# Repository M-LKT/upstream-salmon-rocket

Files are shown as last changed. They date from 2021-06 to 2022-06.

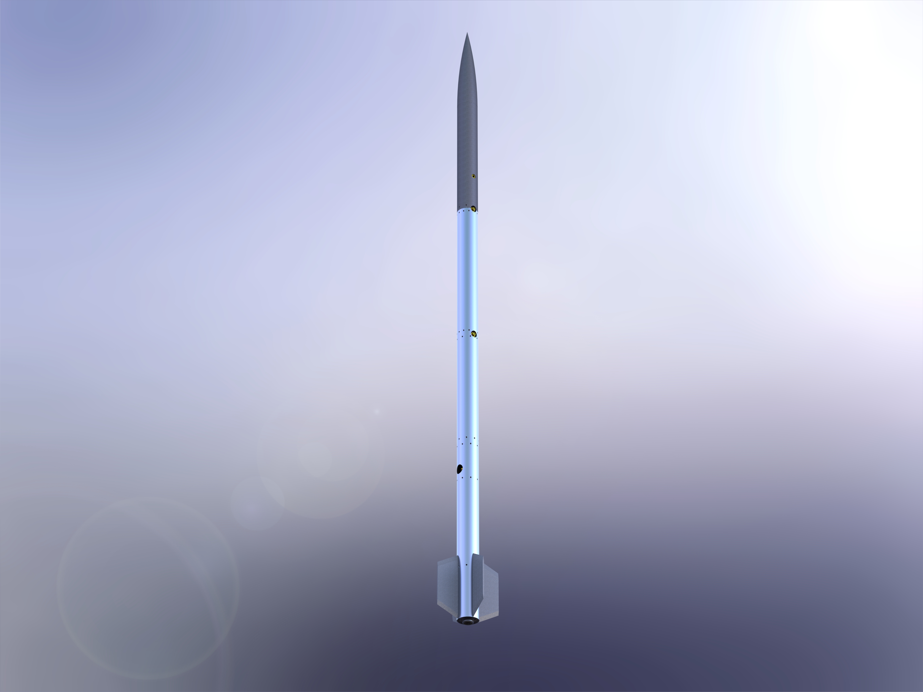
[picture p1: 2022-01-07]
renders/design-beta_v1.0.JPG

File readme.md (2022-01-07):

# Interfaces for Your Engine -> MicroLiquid Vehicle

## Dimensions
- Rocket Tube OD: 2in
- Rocket Tube Thickness: 0.049in
- Standard Skin Fastener: [M2x0.4 Countersunk Torx](https://www.mcmaster.com/92703A146/), 8mm; 8X or 12X
- 

# Other values
- Nitrogen initial pressure: ~1000psi
- Flow control orifice (you choose): [Threaded Flow Control Orifice with Brass Body Plug with Hex Socket, 1/8 NPT Male](https://www.mcmaster.com/2712T51/) (might switch to UNF thread based on burst disk design)
- Target Liftoff TWR: 5
- Estimated takeoff weight: 8.5 lb
- Estimated dry weight: 5 lb

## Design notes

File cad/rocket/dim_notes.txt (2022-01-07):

0.528117in center - vent
0.240000in inlet - vent
0.026500in extra pneu fit gap to piston
1.3745in bore depth
ORB 3/8-24

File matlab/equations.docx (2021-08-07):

Mass lost over time:

m(t)= ∫_0^t (dm)/(dt) dt=̇_0^t m dt

Mass flowrate with pressure:

m=ρQ=ρC_d A√(2Δp)

Pressure with mass

p=(p_i V_i)/V=(p_i V_i)/(V_i +m/ρ)

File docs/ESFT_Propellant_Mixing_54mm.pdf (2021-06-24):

# Eagle Space Flight Team 54mm Propellant Mixing Procedure

### Rev. 1 – 2/25/15

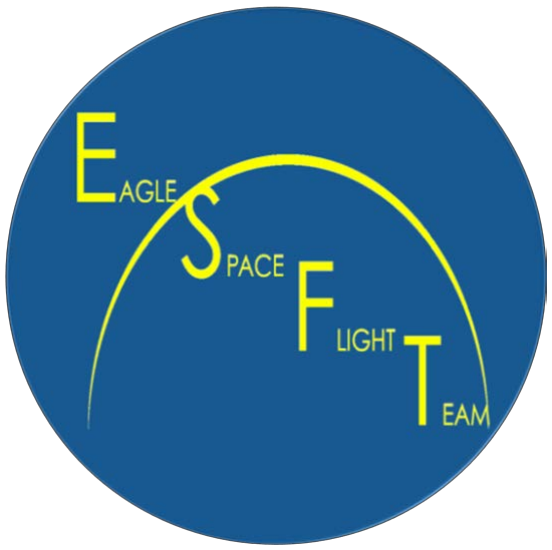
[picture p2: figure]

## Introduction

This document is a procedure for the mixing and processing of large (multiple pounds) batches of ammonium perchlorate composite propellant (APCP) for use in amateur rocket motors. Its purpose is to provide a means for the Propulsion Group of the Eagle Space Flight Team (ESFT) to safely produce a consistent, reliable solid rocket propellant for use on ESFT’s rocket test flights leading up to and including an attempt at a suborbital spaceflight. This version of the document, specifically, is tailored to the mixing and processing of propellant for the 54mm -diameter motors we will use to perform a ballistic characterization of our propellant. These motors will each contain approximately 2lb of propellant, and each individual motor will be mixed as one batch of propellant.

## Method

For mixing the propellant, the team will use a 6qt KitchenAid mixer. Its powerful motor, sturdy construction, and reliability have made this particular mixer the standard in amateur rocketry circles. To avoid generating excess heat during mixing, the mixer is run at a moderate speed, just fast enough to prevent the thickness of the propellant from causing the motor to seize and burn out.
After mixing, the bowl of propellant will be fitted with an acrylic lid attached to a vacuum pump. The vacuum pump will then be used to pull a light vacuum on the contents of the mixing bowl. This will remove any air bubbles introduced into the propellant during mixing as well as any trapped gas from the curing process of the propellant’s binder.
After vacuum processing, the propellant will be packed into cardboard casting tubes with an aluminum mandrel in the center. Each propellant grain will be cast individually, eliminating the need for any cutting or drilling of the propellant after curing.

## Safety

Safety of those working with propellant is the highest priority of any propellant manufacturing operation. During the entire propellant mixing process, all personnel will wear eye protection. Those working directly with propellant chemicals will wear nitrile gloves, and all personnel will wear dust masks during the measuring and incorporation of the dry components of the propellant. Those working directly with propellant will wear non-loose fitting clothing made of cotton or wool (No synthetics!), and long hair will be tied back.
In order to account for the extremely unlikely event of the propellant igniting during mixing, the mixer will not be located inside while it is running. Instead, it will be located a safe distance from the building on the end of an extension cord. The mixer’s speed will be set with it powered off. It will then be switched on and off by inserting and removing the end of the extension cord plugged into a wall socket a safe distance away.
In order to keep dust to a minimum, dry propellant chemicals will be added with the mixer powered off and gently incorporated by hand until they are sufficiently wetted out to prevent any dust from being kicked up when the mixer is restarted. No team members will stand near the mixer while it is switched on and off, and monitoring of the mixing process will take place with a Lexan blast shield between any personnel and the mixer.
During all mixing operations, one person will constantly man a chemical fire extinguisher (No water-filled “pump cans”!), and another will man the point where the extension cord plugs into a wall outlet. In the extremely unlikely event of the propellant igniting during mixing, all team members will move away from the mixer and the person manning the wall outlet will immediately power off the mixer. The mixer, which will be a safe distance from any structures or personnel, will then be allowed to burn until all propellant in the mixing bowl has been consumed. It is only at that time that the person with the fire extinguisher will attempt to put out any remaining fires fueled by parts of the mixer itself.
After mixing, vacuum processing, and packing of the propellant is complete, it will be allowed to cure in a fire cabinet designated for solid rocket propellant and other self-oxidizing materials. After the propellant has cured and the mandrel has been removed, the propellant will continue to be stored in the same cabinet until it is needed for static testing or flight. Mix sessions will be scheduled such that this storage interval is as short as is feasible.

## Personnel

The personnel present for any mixing session will be assigned to one of the following duties.

- Chemical Measuring: Weighs out precise amounts propellant chemicals into temporary containers before mixing starts. This makes the mixing operation itself run more smoothly.
- Ingredient Incorporation/Mix Observer: Adds propellant chemicals to mixing bowl one at a time in the order presented later in this document. Occasionally checks propellant during mixing to ensure that it is being mixed thoroughly enough to produce a consistent product.
- Mixer Power Operator: Mans the location where the mixer plugs into a wall outlet. Switches mixer on and off as needed during mixing and remains ready to switch off mixer in unlikely event of propellant ignition.
- Fire Extinguisher Operator: Stands ready with fire extinguisher. In unlikely event of propellant ignition, they will wait until propellant has been fully consumed before extinguishing remains of mixer.
- Safety Observer: Watches area surrounding mixing operation for safety hazards. Keeps unrelated personnel a safe distance away from mixing operation.
The setup for propellant mixing will be arranged similarly to the diagram on the next page.

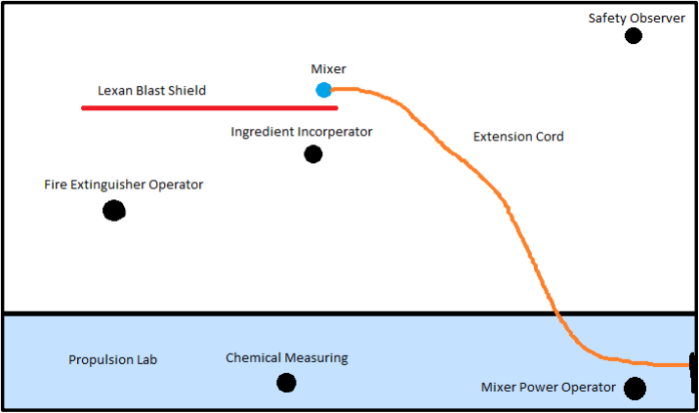
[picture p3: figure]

In this setup, all personnel have either a blast shield, building wall, or sufficient offset distance between themselves and the mixer at all times. Sufficient offset distance is considered to be at least 30ft without a blast shield or wall.

## Procedure

### Propellant Formula

The propellant formula to be used by the team consists of the following components.

- 200µ Ammonium Perchlorate: The propellant’s oxidizer
- 20µ Atomized Spherical Aluminum Powder: The propellant’s fuel
- 5µ Oxamide: Burn rate suppressant.
- R-45M Hydroxyl-terminated Polybutadiene Resin (HTPB): The propellant’s binder. Also serves as a fuel.
- Desmodur E744/MDI Isocyanate: Curative for the HTPB.
- Isodecyl Pelargonate (IDP): Plasticizer for the HTPB.
- Silicone Oil: Anti-foaming agent/surfactant.
Before mixing, all personnel working with propellant must read and familiarize themselves with the MSDSs for the propellant chemicals.
These chemicals are to be mixed in the following proportions, each percentage being a portion of the desired mass of propellant to be mixed.

- Ammonium Perchlorate: 72%
- Aluminum: 7%
- Oxamide: 3%
- HTPB: 14.08%
- E744/MDI: 2.12%
- IDP: 1.8%
- Silicone Oil: One drop per kilogram of propellant being mixed

### Equipment

The following equipment is needed for each propellant mix session.

- Safety glasses
- Dust masks
- Nitrile gloves
- Lexan blast shield
- Chemical fire extinguisher
- 6qt mixer fitted with paddle
- Mixing bowl corresponding to mixer
- Ice cream spade
- Extension cord, minimum length 30’
- Vacuum pump
- Plexiglas lid fitted to bowl with fitting for vacuum pump
- Core mandrel
- Casting tube caps
- Casting tube
- Metal or wood packing rod
- Mold release spray
- Paper towels
- Mineral spirits
- Metal “burn bucket”

### Procedure

Read through this procedure in its entirety before beginning to mix!
The process of mixing propellant is both time sensitive and unforgiving of mistakes. It is imperative that all personnel know exactly what tasks to perform and exactly when to perform them.
Throughout this procedure, important safety notes will appear in boxes such as this one. Important procedural notes will appear bolded within the text.
1. Set up the mixer, extension cord, blast shield, and fire extinguisher as shown in the figure earlier in this document.

2. Cut casting tube to desired grain length. Spray coring rod and casting tube caps with mold release. Insert coring rod into bottom (non-vented) casting tube cap before sliding the casting tube over the core mandrel and seating it in the cap. Do not get mold release on the inside of the casting tube. A thorough bond between the propellant and the inside of the casting tube is imperative to proper motor operation.
The tube should fit snugly into the cap. If the casting tube fits loosely in the cap, wrap a few layers of masking tape around the bottom of the tube. If the casting tube will not fit, lightly sand the bottom of the tube.

If not wearing them already, all personnel don safety glasses at this time. All personnel in the chemical measuring area don nitrile gloves and dust masks at this time.

3. If you have not done so already, use the percentages in the propellant formula earlier in the document to calculate the mass of each component needed for the desired amount of propellant to be mixed. Double and triple check your calculations before moving forward.
4. Measure the ammonium perchlorate, aluminum, oxamide, curative, and plasticizer into separate disposable containers.

Ammonium perchlorate and aluminum are never to be allowed to come into contact without the binder!
The binder acts as a burn rate suppressant for the ammonium perchlorate/aluminum mixture and also increases the activation energy of the propellant. With the binder, this mixture will burn at approximately the same rate as office paper and requires a substantial energy input to ignite. Without the binder, the mixture is virtually identical to pyrotechnic flash powder, possessing a fast burn rate and sensitivity to friction and physical shock.
5. Measure out the HTPB resin. This ingredient can be measured directly into the mixing bowl. Next, add the plasticizer and silicone oil into the bowl. Do not stir the contents of the bowl at this time. The goal is to create a pool of plasticizer on top of the resin.
6. The aluminum is then added to the bowl by pouring it into the pool of plasticizer. When pouring in the aluminum, keep its container low over the surface of the liquid in order to keep dust to a minimum. Allow the plasticizer to soak into the aluminum until it is completely wetted out. Then, gently incorporate the aluminum into the mixture by hand using the ice cream spade. Do not move on to the next step until the aluminum powder is completely wetted out and evenly distributed within the HTPB. The container into which the aluminum was measured is then discarded in normal garbage.
7. The oxamide is then added to the bowl in the same manner as the aluminum, taking care with dust prevention. It is then incorporated into the mixture by hand. The container into which the oxamide was measured is then discarded into normal garbage.

From this point on, all waste will be disposed of in the burn bucket.
Waste which has not come into contact with ammonium perchlorate is safe to dispose of in normal garbage, but any oxidizer-contaminated waste must be disposed of in the burn bucket. This waste will be burned before disposal. The procedure for burning this waste is outlined later in this procedure.
8. Approximately one third of the ammonium perchlorate is added to the bowl at this time, employing the same dust prevention practices used with the other solid components. The ammonium perchlorate is then wetted out and incorporated into the mixture by hand as before.
9. Another third of the ammonium perchlorate is then added to the bowl and wetted out by hand.
10. The final third of the ammonium perchlorate is then added to the bowl and wetted out by hand. The bowl is then placed in the mixer which is then switched on and allowed to mix the propellant for ten minutes. During this process, the mixing is stopped every few minutes in order to scrape down the sides of the mixing bowl.
11. The mixer is then stopped and the E744/MDI is added to the bowl. The mixer is then restarted and allowed to mix the propellant for 10 minutes, stopping every few minutes to scrape down the sides of the bowl.
12. The bowl is then removed from the mixer. The vacuum lid is placed on the bowl and the vacuum pump is switched on and allowed to pull vacuum on the propellant for five minutes.
13. The pump is switched off and the lid is removed. The propellant is then pulled from the bowl, rolled into “clay snakes”, and dropped into the casting tube. Occasionally, the packing rod is used to tamp down the propellant. With the packing rod, the goal is not to mash the propellant into the tube, but rather to ensure a well-packed, uniform propellant with no voids present in the grains.
14. Once the casting tube has been filled, the top (vented) casting tube cap is slid over the mandrel and seated on the top of the casting tube. If multiple grains are being cast, the next casting tube (already fitted with a non-vented bottom cap) is slid onto the mandrel and propellant packing proceeds as with the first grain.
15. Once all propellant is packed, the casting setup is placed in a fire cabinet and allowed to cure. This process will usually take a few days.
16. The mixing bowl, mixer paddle, ice cream spade, and packing rod are all thoroughly cleaned with paper towels and mineral spirits. These paper towels and any scrap propellant are disposed of in the burn bucket. After cleanup is complete, no propellant residue whatsoever may remain on any tools or equipment.

17. After cleanup is complete, the burn bucket is taken to a remote area away from combustible materials. Its contents are then ignited either electronically or using a fuse and allowed to burn completely. The ashes left over are then doused with water and disposed of in normal garbage.

Firefighting measures must be in place when burning the contents of the burn bucket!
This includes at least two people and at least one chemical fire extinguisher. Shovels and/or rakes are also useful for firefighting.
18. After three to five days, the propellant should be fully cured. The casting tube caps can now be removed and the core mandrels pulled out of the grains. The propellant is to be stored in a fire cabinet until use.

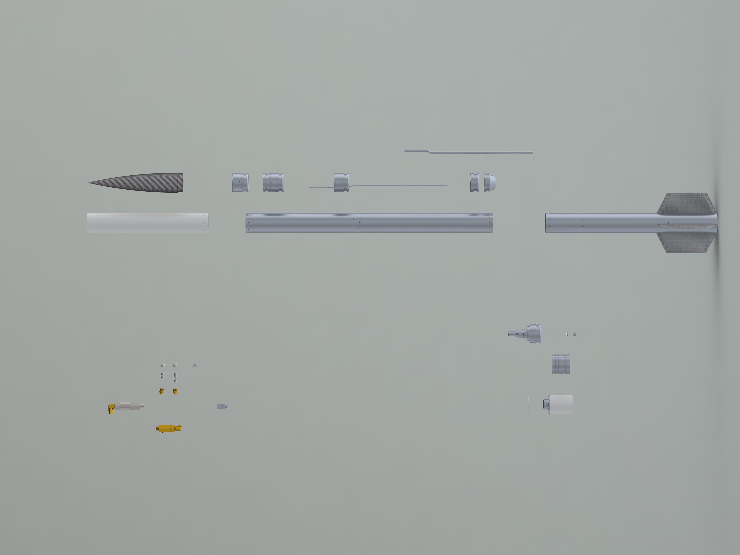
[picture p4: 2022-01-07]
renders/exploded.JPG

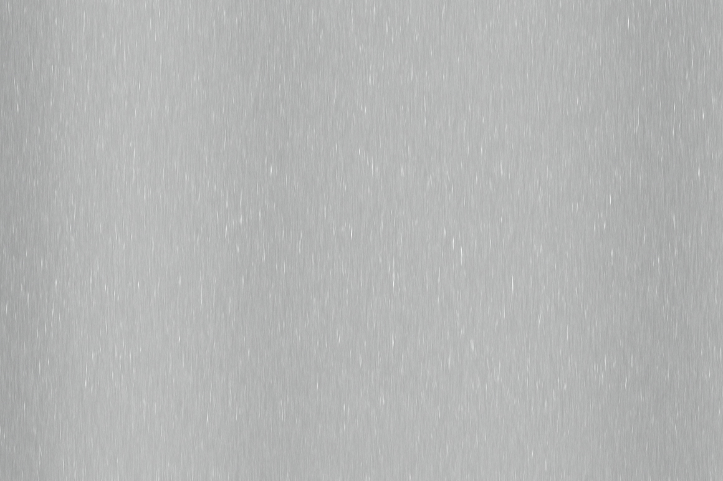
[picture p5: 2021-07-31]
vehicle-sims/aluminum-texture-1.jpg

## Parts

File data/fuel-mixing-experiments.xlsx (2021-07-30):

Type | Salmon Mass | IPA Mass | Salmon % | Total Mass | Pre-Mix Vol | Mix Time | Post-Mix Vol | Post-Mix Mass | Notes | Density
F/W | g | g | ratio | g | mL | s | mL | g
F | 41.4 | 55.2 | 0.4285714286 |  |  |  | 25 | 21 |  | 0.84
 |  | 61.7 | 0 |  |  |  | 30 | 27.8 |  | 0.9266666667
 |  |  | #DIV/0!
 |  |  | #DIV/0!
 |  |  | #DIV/0!
 |  |  | #DIV/0!
 |  |  | #DIV/0!
 |  |  | #DIV/0!

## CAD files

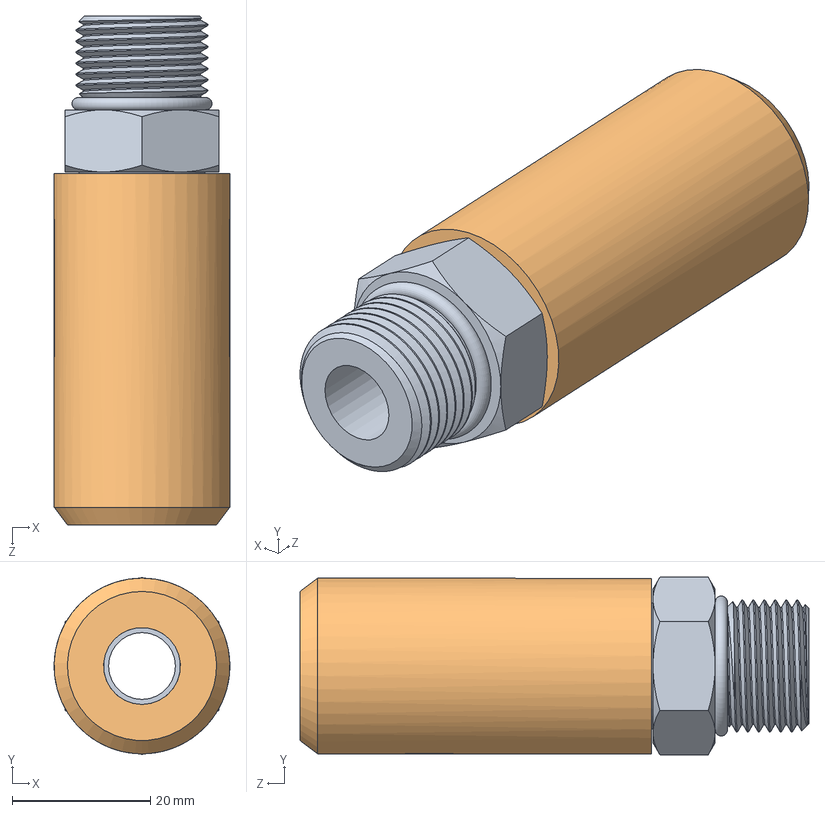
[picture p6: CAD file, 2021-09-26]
cad/burst_disk/normal_burst.SLDASM
25.4 x 25.7 x 73.5 mm
6407T859_O-Ring Face Seal Fitting
test_burst-disk

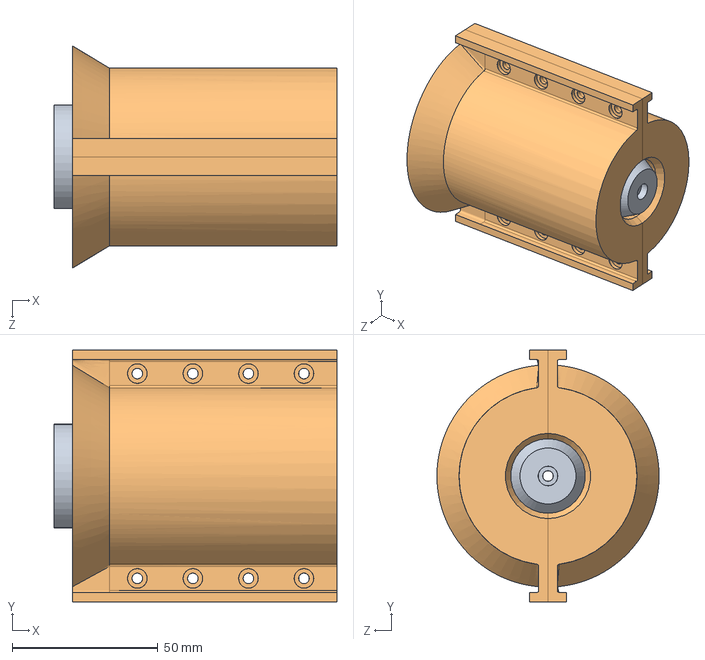
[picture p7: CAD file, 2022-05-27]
cad/engines/mold.SLDASM
97.0 x 86.4 x 76.2 mm
cast-with-nozzle_MOLD_chamber-core
cast-with-nozzle_MOLD_outer x 2

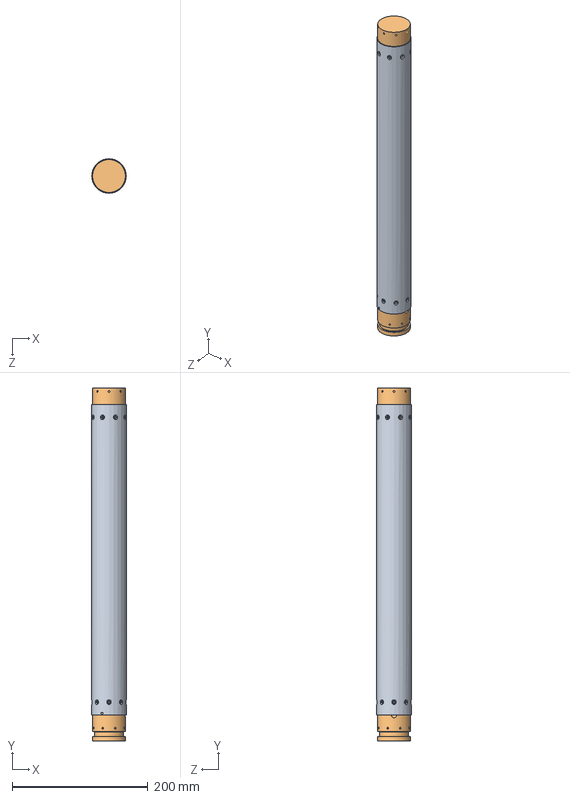
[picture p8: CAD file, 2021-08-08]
cad/rocket/sw_fea/press-sim-assy.SLDASM
50.8 x 519.4 x 50.8 mm
tube
spacer x 2

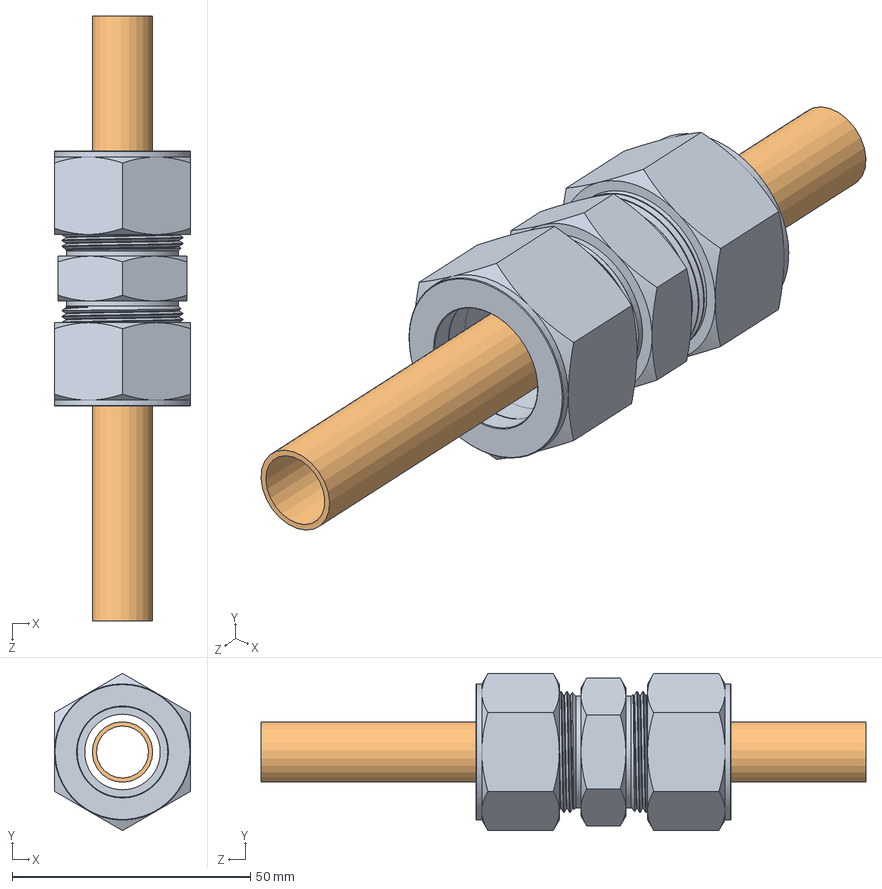
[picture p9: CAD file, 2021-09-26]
cad/burst_disk/concentric_burst.SLDASM
28.6 x 33.0 x 127.0 mm
5182K722_Yor-Lok Fitting for Stainless Steel Tubing
0.5-tube

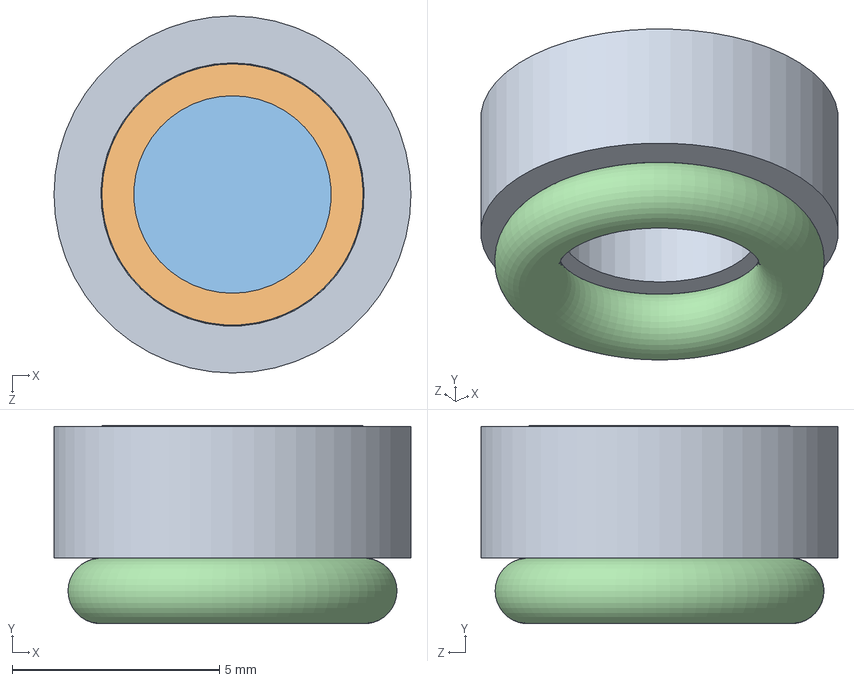
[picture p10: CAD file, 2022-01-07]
cad/rocket/burst_disk/Burst_Assembly.SLDASM
8.61 x 4.78 x 8.61 mm
burst-housing
disk-compressor
disk-proxy
AS568-006-O-Ring

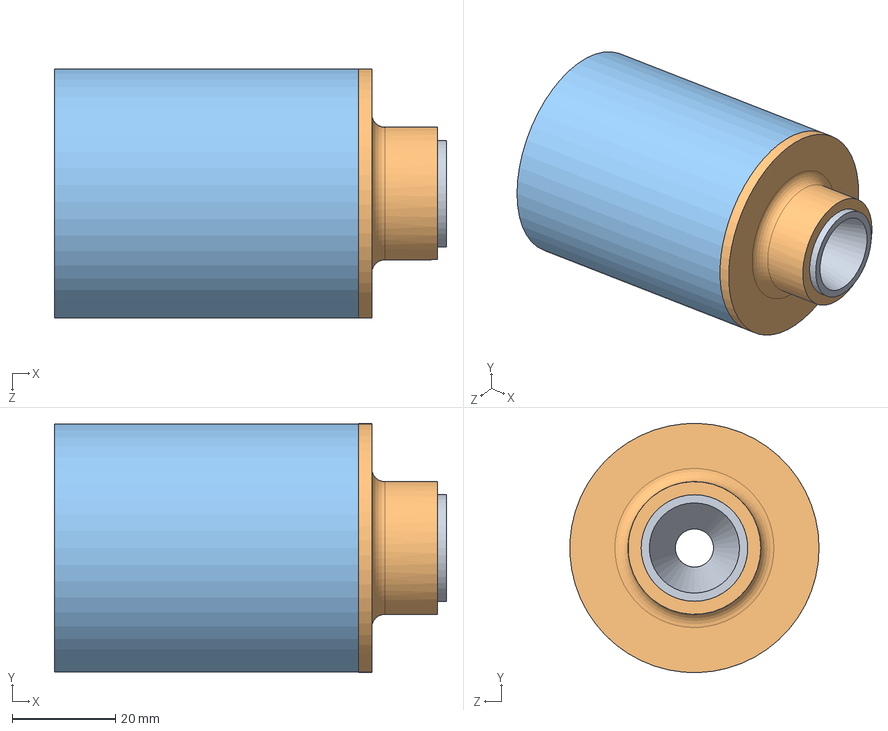
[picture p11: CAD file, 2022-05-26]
cad/engines/Engine-Retainer_config.SLDASM
76.0 x 48.3 x 48.3 mm
RCS-0.291-Nozzle
retainer-cap^Engine-Retainer_config
cast-with-nozzle

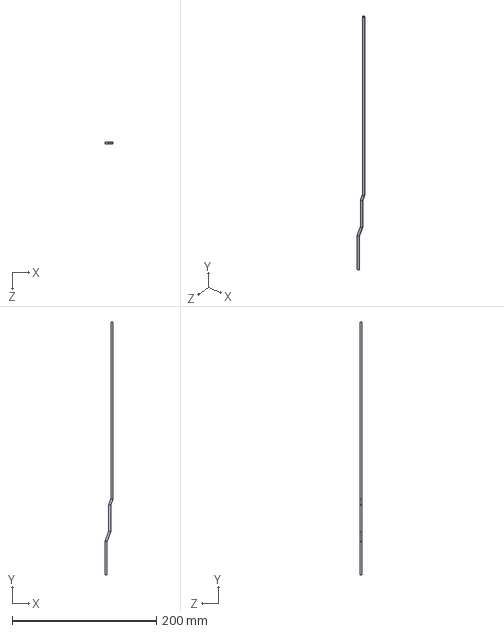
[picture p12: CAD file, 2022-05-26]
cad/rocket/Tube_2-Rocket.SLDASM
11.3 x 350.5 x 3.18 mm

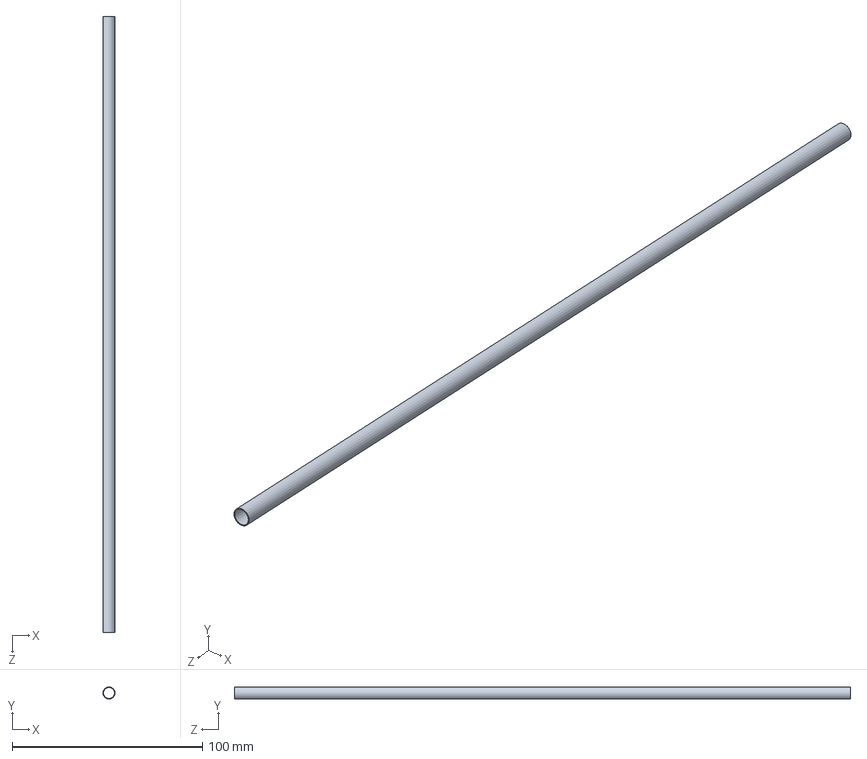
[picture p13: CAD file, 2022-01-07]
cad/rocket/main-lox-tube.SLDPRT
6.35 x 6.35 x 323.9 mm

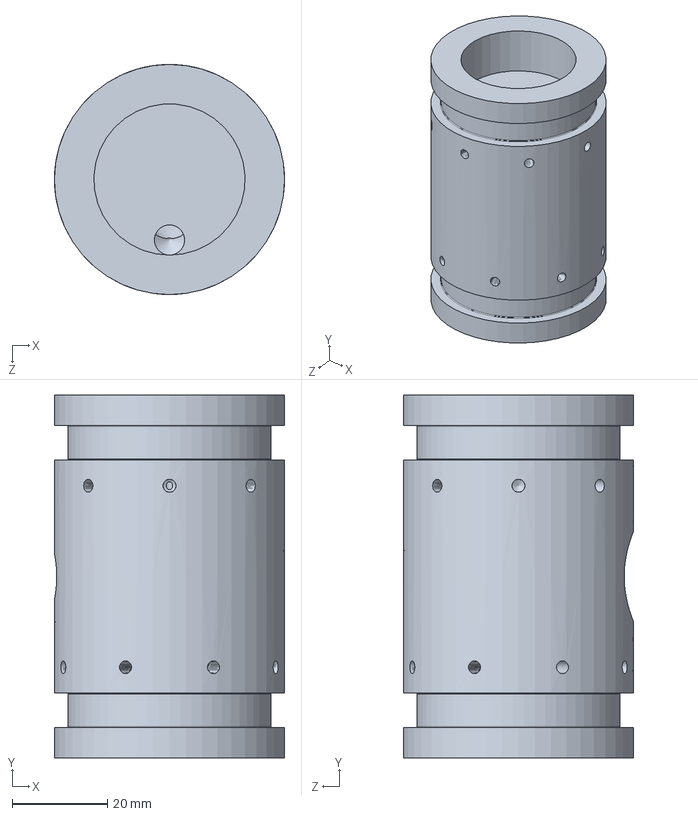
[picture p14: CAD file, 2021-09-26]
cad/rocket/valve_test_assy.SLDASM
48.3 x 76.2 x 48.3 mm
spacer
ball
seat x 2
valve-cap

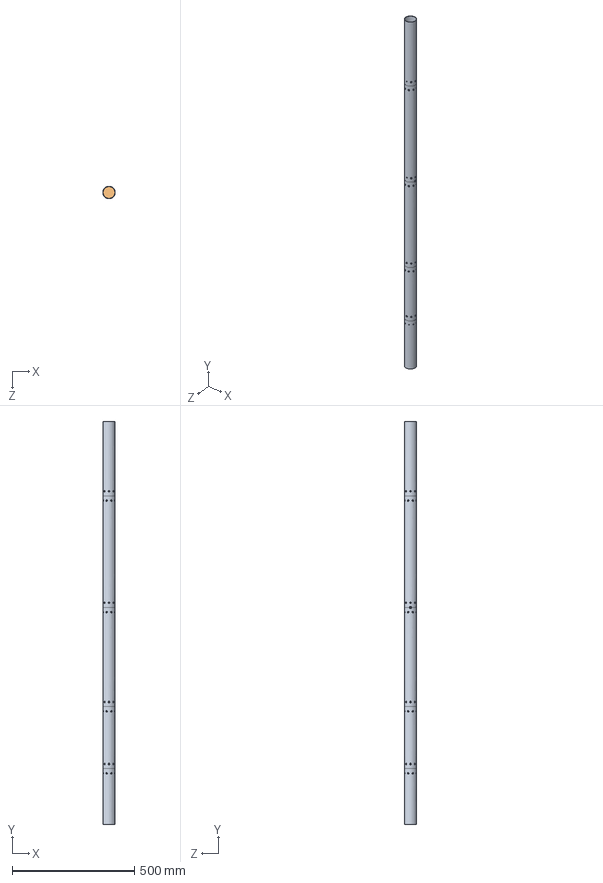
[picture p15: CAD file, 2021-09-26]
cad/rocket/Rocket.SLDASM
50.8 x 1651.0 x 50.8 mm
tube x 5
spacer x 4
94355A231_NONMARRING FLAT POINT SOCKET SET SCREW (5-16 length)
94564A405_NYLON HEX SOCKET FLAT POINT SET SCREW
pyro-valve-piston
injector
ablative-chamber

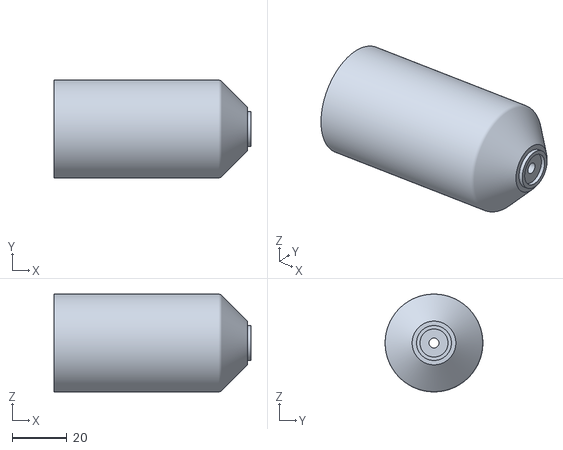
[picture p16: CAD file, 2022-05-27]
cad/engines/mold-with-nozzle-v2/BOTTOM-cast-with-nozzle_MOLD_chamber-core.STL
71.6 x 35.6 x 35.6

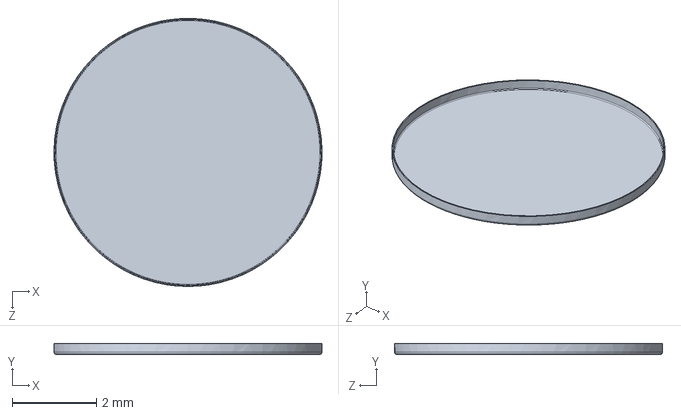
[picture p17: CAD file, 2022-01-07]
cad/rocket/burst_disk/disk-proxy.SLDPRT
6.35 x 0.254 x 6.35 mm

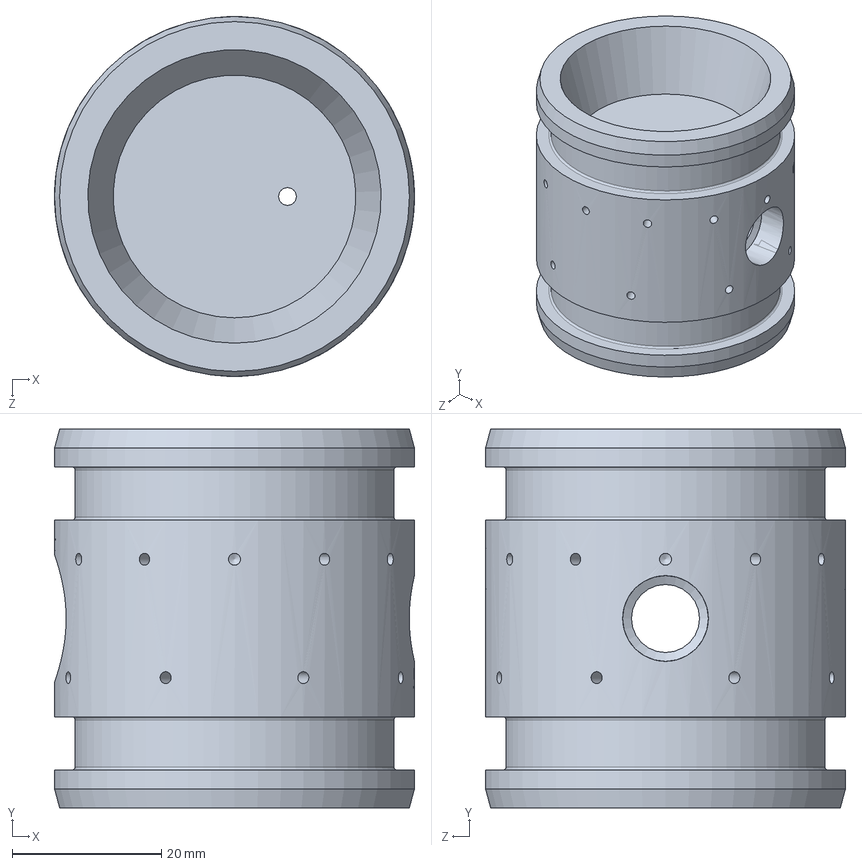
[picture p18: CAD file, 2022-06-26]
cad/rocket/spacer.SLDPRT
48.3 x 50.8 x 48.3 mm

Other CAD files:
cad/rocket/Tube_4-Rocket.SLDASM
cad/rocket/Auto-Main_LOX-Rocket.SLDASM
cad/rocket/Tube_3-Rocket.SLDASM
cad/rocket/Tube_3-Rocket-001.SLDASM
cad/rocket/Tube_1-Rocket.SLDASM
cad/burst_disk/0.5-tube.SLDPRT
cad/burst_disk/5182K722_Yor-Lok Fitting for Stainless Steel Tubing.SLDPRT
cad/burst_disk/6407T859_O-Ring Face Seal Fitting.SLDPRT
cad/burst_disk/test_burst-disk.SLDPRT
cad/cots/2333N129_Nickel-Plated Brass Push-to-Connect Fitting.SLDPRT
cad/cots/2712T655_Threaded Flow Control Orifice with Brass Body.SLDPRT
cad/cots/2712T666_Threaded Flow Control Orifice with Brass Body.SLDPRT
cad/cots/2840K21_316 Stainless-Steel Panel-Mount On Off Valve.SLDPRT
cad/cots/2840K23_316 Stainless-Steel Panel-Mount On Off Valve.SLDPRT
cad/cots/4112T53_Compact High-Pressure Brass Ball Valve.SLDPRT
cad/cots/4114T43_Brass Panel-Mount On Off Valve.SLDPRT
cad/cots/4118T114_Panel-Mount On Off Valve.SLDPRT
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

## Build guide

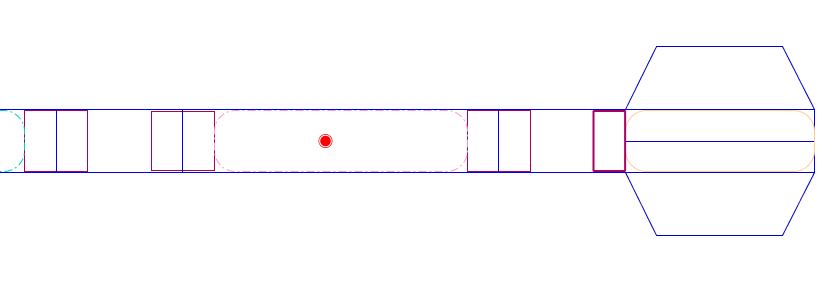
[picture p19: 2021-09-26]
cad/burst_disk/lower_assembly.png

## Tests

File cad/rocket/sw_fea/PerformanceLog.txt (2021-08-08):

Number of Contacts: 4
Number of contact data: 12992

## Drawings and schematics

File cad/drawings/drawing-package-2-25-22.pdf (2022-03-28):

2

B

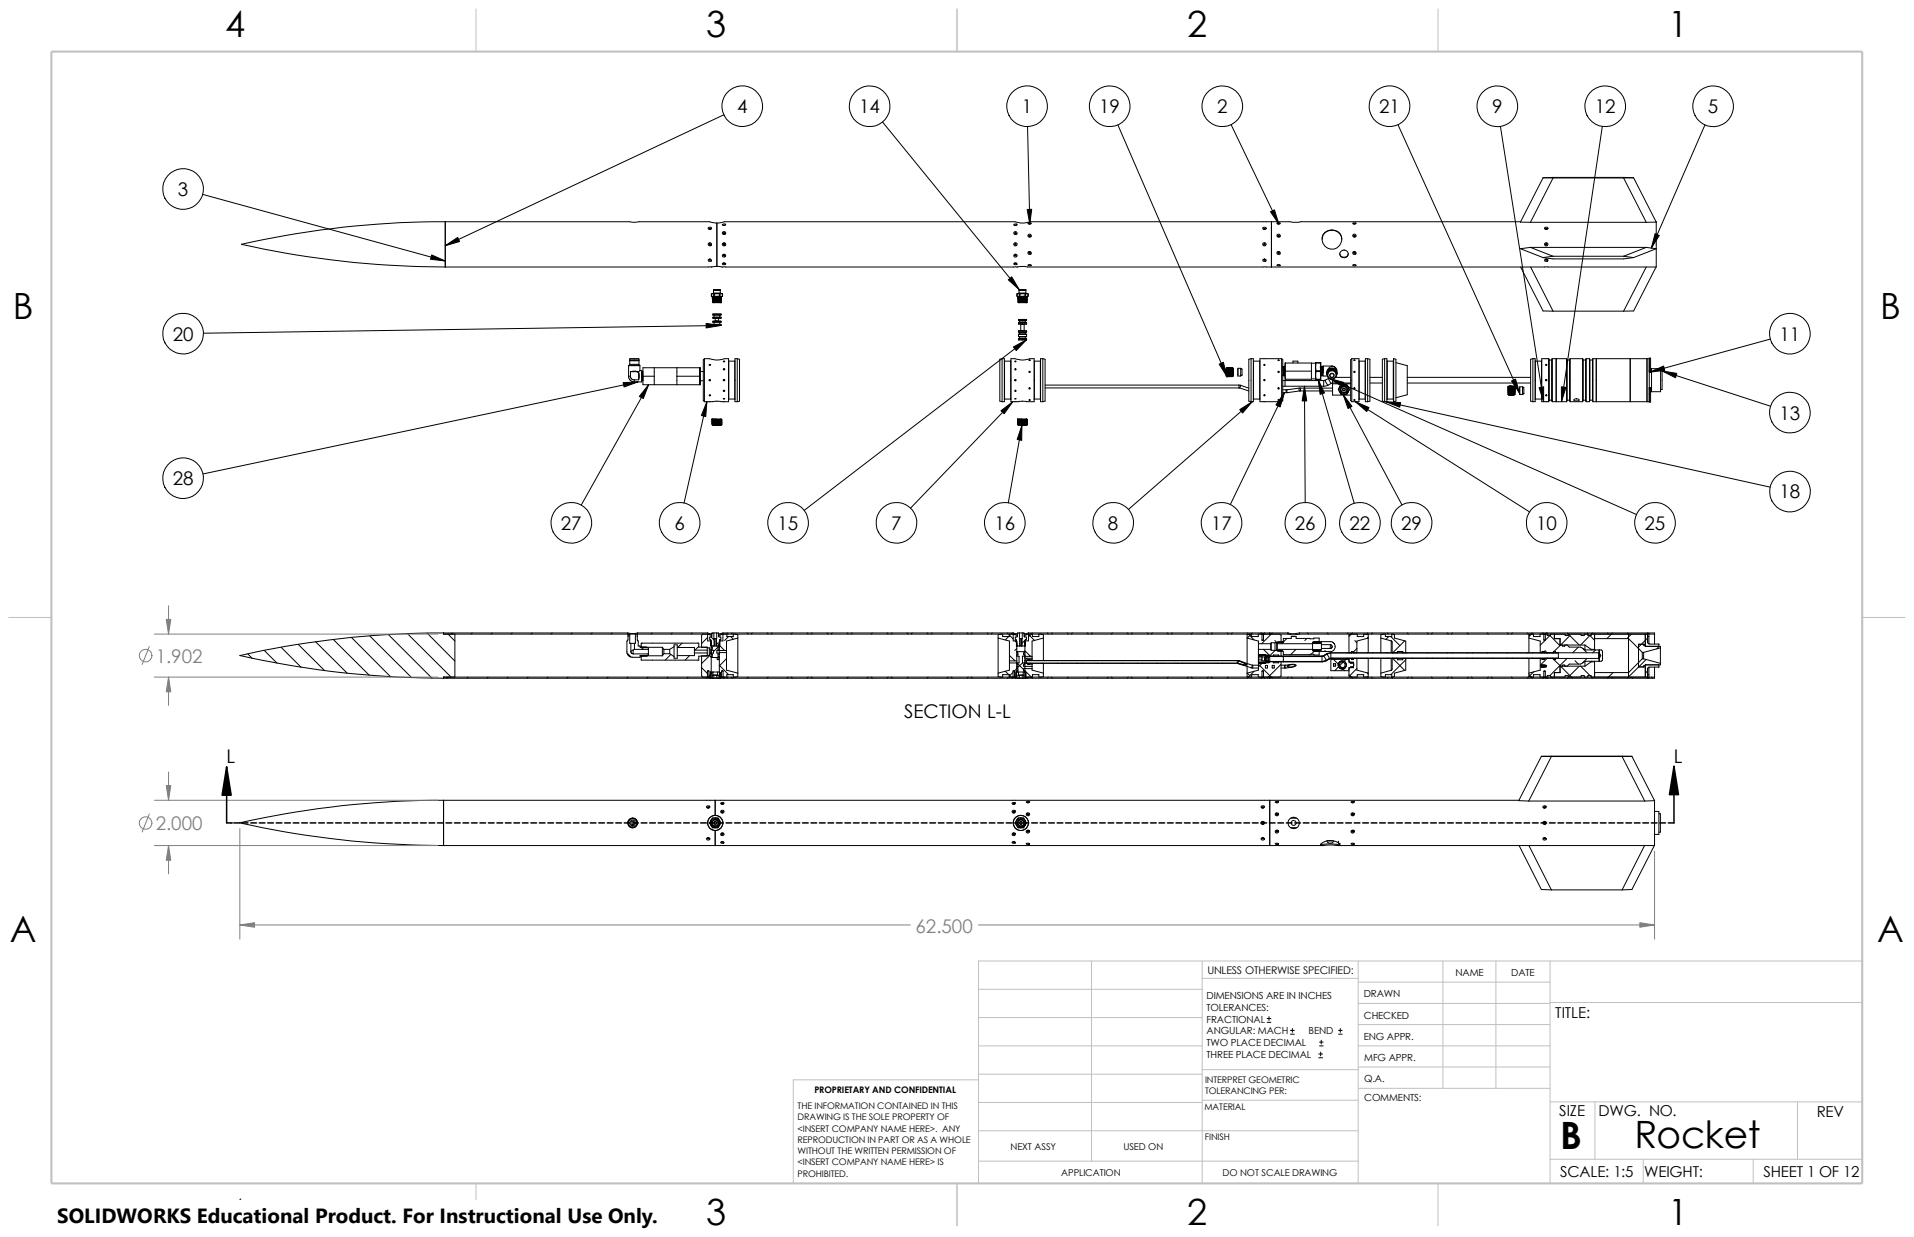
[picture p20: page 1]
SHEET 1 OF 12; SCALE: 1:5; WEIGHT:; COMMENTS:; PROHIBITED.; APPLICATION; SECTION L-L

UNLESS OTHERWISE SPECIFIED: | | NAME | DATE

DIMENSIONS ARE IN INCHES TOLERANCES: FRACTIONAL ANGULAR: MACH BEND TWO PLACE DECIMAL THREE PLACE DECIMAL | DRAWN

CHECKED | | | TITLE:

ENG APPR.
MFG APPR.

INTERPRET GEOMETRIC TOLERANCING PER: | Q.A.
MATERIAL | | SIZE B | DWG. NO. Rocket | REV

PROPRIETARY AND CONFIDENTIAL
THE INFORMATION CONTAINED IN THIS
DRAWING IS THE SOLE PROPERTY OF
<INSERT COMPANY NAME HERE>. ANY
REPRODUCTION IN PART OR AS A WHOLE
WITHOUT THE WRITTEN PERMISSION OF
<INSERT COMPANY NAME HERE> IS

NEXT ASSY | USED ON | FINISH

DO NOT SCALE DRAWING

SOLIDWORKS Educational Product. For Instructional Use Only.

B B

ITEM NO. | PART NUMBER | DESCRIPTION | QTY. | ITEM NO. | PART NUMBER | DESCRIPTION | QTY.

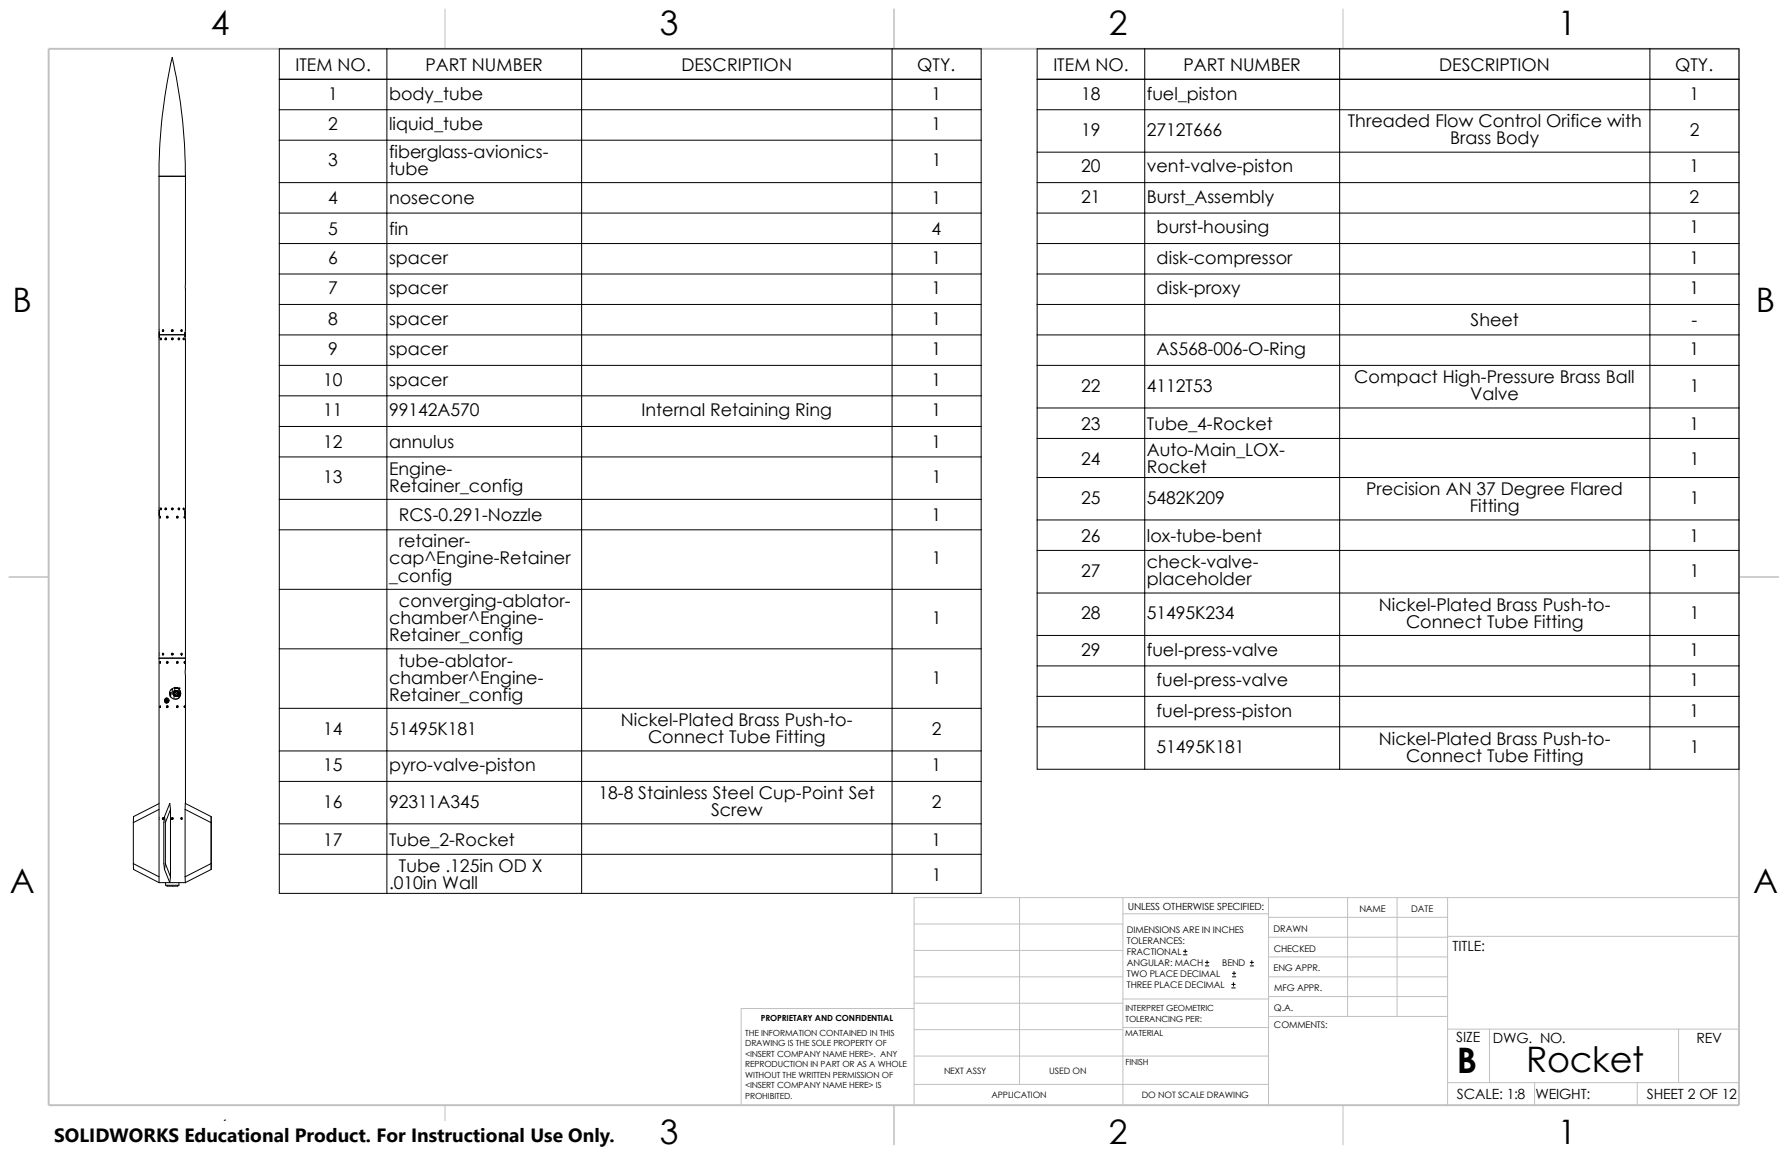
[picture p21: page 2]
Rocket; SHEET 2 OF 12; SCALE: 1:8; WEIGHT:; DWG. NO.; REV; SIZE; COMMENTS:; MATERIAL; APPLICATION; PROHIBITED.

1 | body_tube | | 1 | 18 | fuel_piston | | 1
2 | liquid_tube | | 1 | 19 | 2712T666 | Threaded Flow Control Orifice with Brass Body | 2
3 | fiberglass-avionics-tube | | 1

20 | vent-valve-piston | | 1

4 | nosecone | | 1 | 21 | Burst_Assembly | | 2
5 | fin | | 4 | | burst-housing | | 1
6 | spacer | | 1 | | disk-compressor | | 1
7 | spacer | | 1 | | disk-proxy | | 1
8 | spacer | | 1 | | | Sheet | -
9 | spacer | | 1 | | AS568-006-O-Ring | | 1
10 | spacer | | 1 | 22 | 4112T53 | Compact High-Pressure Brass Ball Valve | 1
11 | 99142A570 | Internal Retaining Ring | 1
12 | annulus | | 1
13 Engine- | Retainer_config | | 1

23 | Tube_4-Rocket | | 1
24 Auto-Main_LOX- | Rocket | | 1
25 | 5482K209 | Precision AN 37 Degree Flared Fitting | 1

RCS-0.291-Nozzle | | 1
retainer-cap^Engine-Retainer _config | | 1

26 | lox-tube-bent | | 1
27 check-valve- | placeholder | | 1

converging-ablator-chamber^Engine-Retainer_config | | 1

28 | 51495K234 | Nickel-Plated Brass Push-to-Connect Tube Fitting | 1

29 | fuel-press-valve | | 1

tube-ablator-chamber^Engine-Retainer_config | | 1

fuel-press-valve | | 1
fuel-press-piston | | 1
51495K181 | Nickel-Plated Brass Push-to-Connect Tube Fitting | 1

14 | 51495K181 | Nickel-Plated Brass Push-to-Connect Tube Fitting | 2

15 | pyro-valve-piston | | 1
16 | 92311A345 | 18-8 Stainless Steel Cup-Point Set Screw | 2

17 | Tube_2-Rocket | | 1

Tube .125in OD X .010in Wall | | 1

UNLESS OTHERWISE SPECIFIED: | | NAME | DATE

DIMENSIONS ARE IN INCHES TOLERANCES: FRACTIONAL ANGULAR: MACH BEND TWO PLACE DECIMAL THREE PLACE DECIMAL | DRAWN

CHECKED | | | TITLE:

ENG APPR.
MFG APPR.

INTERPRET GEOMETRIC TOLERANCING PER: | Q.A.

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

B B

1.282

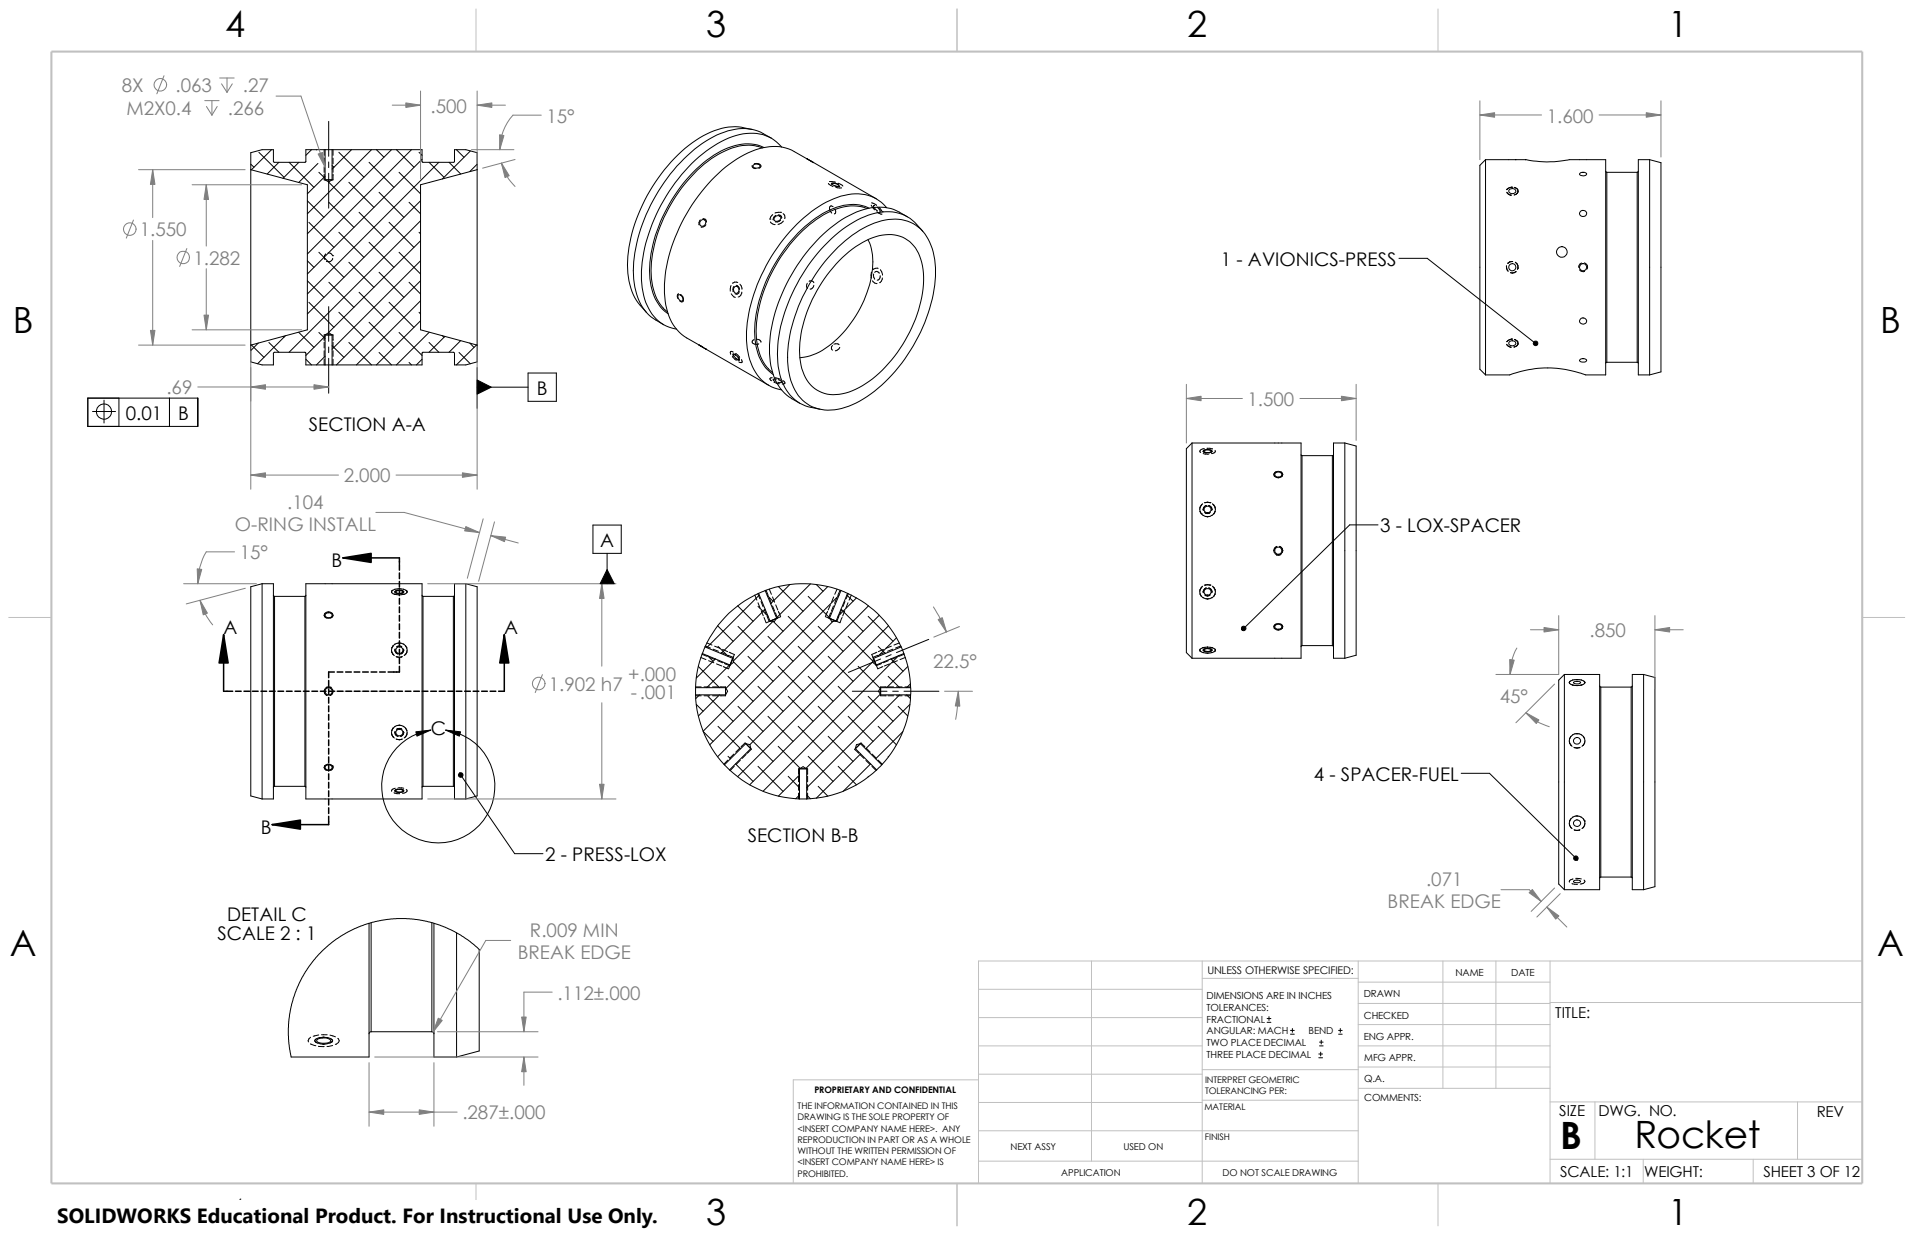
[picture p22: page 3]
Rocket; SHEET 3 OF 12; SCALE: 1:1; WEIGHT:; DWG. NO.; REV; SIZE; COMMENTS:; MATERIAL; 0.01 SECTION A-A B; 2 - PRESS-LOX; .104 O-RING INSTALL; 4 - SPACER-FUEL; .071 BREAK EDGE; 1 - AVIONICS-PRESS; SECTION B-B; DETAIL C SCALE 2 : 1; R.009 MIN BREAK EDGE; 3 - LOX-SPACER

UNLESS OTHERWISE SPECIFIED: | | NAME | DATE

DIMENSIONS ARE IN INCHES TOLERANCES: FRACTIONAL ANGULAR: MACH BEND TWO PLACE DECIMAL THREE PLACE DECIMAL | DRAWN

CHECKED | | | TITLE:

ENG APPR.
MFG APPR.

INTERPRET GEOMETRIC TOLERANCING PER: | Q.A.

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

B B

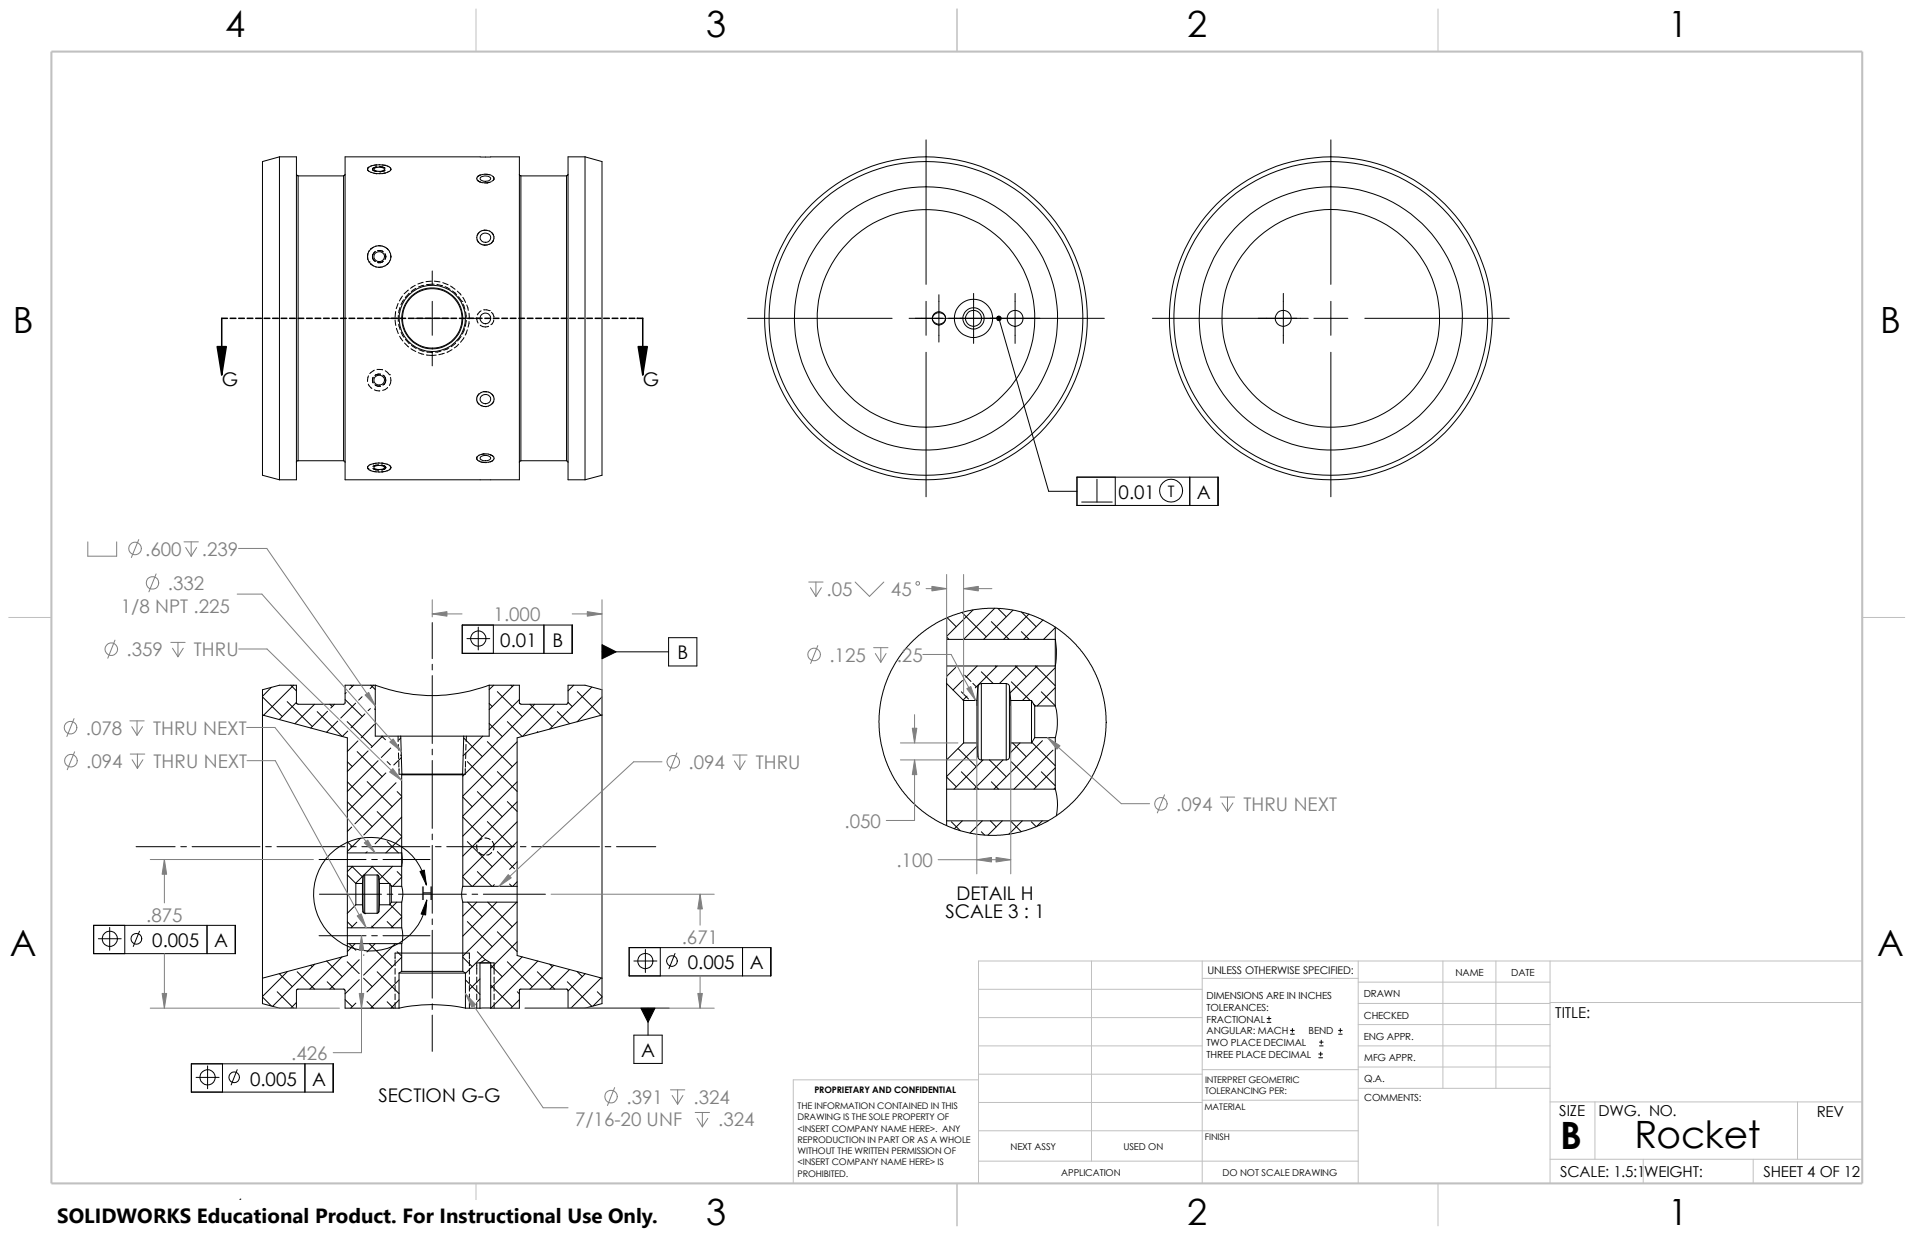
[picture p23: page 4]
Rocket; SHEET 4 OF 12; SCALE: 1.5:1WEIGHT:; DWG. NO.; REV; SIZE; COMMENTS:; MATERIAL; SECTION G-G; THRU NEXT; THRU; .332 1/8 NPT .225; 7/16-20 UNF; DETAIL H SCALE 3 : 1

UNLESS OTHERWISE SPECIFIED: | | NAME | DATE

DIMENSIONS ARE IN INCHES TOLERANCES: FRACTIONAL ANGULAR: MACH BEND TWO PLACE DECIMAL THREE PLACE DECIMAL | DRAWN

CHECKED | | | TITLE:

ENG APPR.
MFG APPR.

0.005 A | | | | | INTERPRET GEOMETRIC TOLERANCING PER: | Q.A.

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

B B
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

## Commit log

2021-06-22 configured tube added
    [Rocket-multipart.SLDASM, tube.SLDPRT]
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2021-06-24 finished prelim mass models
    [Rocket.SLDASM, ablative-chamber.SLDPRT, injector.SLDPRT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]
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2021-07-30 3 inch variant study, added notes for charlie
    [Rocket.SLDASM, spacer.SLDPRT, tube.SLDPRT]
2021-07-30 sizing cost matrix started
    [fuel-mixing-experiments.xlsx, matrix.xlsx]
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2021-07-30 swapped lox and fuel tanks to reflect sizing. started pv combined load analysis
    [Rocket.SLDASM, matrix.xlsx, tube.SLDPRT]
2021-07-31 intermediate sizing changes to thin walls
    [Rocket.SLDASM, ablative-chamber.SLDPRT, matrix.xlsx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]
2021-08-04 matlab blowdown model wip
    [matrix.xlsx]
2021-08-08 first pass flight simulation
    [flight-sim-1-output.csv, matrix.xlsx]
2021-08-08 combined loading von Mises on PV complete
    [flight-sim-1-output.csv, matrix.xlsx]
2021-08-08 leak before break satisfied
    [matrix.xlsx]
2021-08-08 prelim SW FEA for bolt tearout and stress raisers
    [Rocket.SLDASM, matrix.xlsx, nosecone.SLDPRT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]
2021-08-16 working on integrated fill valve
    [4118T114_Panel-Mount On Off Valve.SLDPRT, 4149T41_Diverting Valve.SLDPRT, 45395K136_LOW-PROFILE TYPE 316 SS BALL VALVE.SLDPRT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]
2021-09-26 adding space for burst disks
    [0.5-tube.SLDPRT, 5182K722_Yor-Lok Fitting for Stainless Steel Tubing.SLDPRT, 6407T859_O-Ring Face Seal Fitting.SLDPRT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]
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2021-10-08 downsize engine to 15s runtime
    will have to update matlab model to account for different props and flow discharge coeffs. engine might not be modeled at decreased pressure. mass drop over time linear enough, ok for openrocket
    [Rocket.SLDASM, nosecone.SLDPRT]
2021-10-09 new size and tube config
    [5148K295_High-Pressure D.O.T. Push-to-Connect Fitting.SLDPRT, 51495K181_Nickel-Plated Brass Push-to-Connect Tube Fitting.SLDPRT, 92311A594_18-8 Stainless Steel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]
2021-10-09 new piping layout done
    need to control the god damn LOX lead timing
    [5182K804_Yor-Lok Fitting for Stainless Steel Tubing.SLDPRT, 5182K807_Yor-Lok Fitting for Stainless Steel Tubing.SLDPRT, 5482K111_Precision AN 37 Degree Flared 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]
2021-10-09 fuel piston and fitting configuration
    [50695K61_37 Degree Flared Fitting for Steel Tubing.SLDPRT, 5182K804_Yor-Lok Fitting for Stainless Steel Tubing.SLDPRT, 5182K807_Yor-Lok Fitting for Stainless S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]
2021-10-10 pneu valve sizing complete + thread and brazing change
    [2712T655_Threaded Flow Control Orifice with Brass Body.SLDPRT, 2712T666_Threaded Flow Control Orifice with Brass Body.SLDPRT, 51495K181_Nickel-Plated Brass Pus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]
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2021-11-12 pre 2021 sw roll forward
    [99142A580_Internal Retaining Ring.SLDPRT, COSMETIC_99142A570_Internal Retaining Ring.SLDPRT, Rocket.SLDASM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]
2021-11-26 begin manufacturing drawings, 2021 SW required
    [2712T666_Threaded Flow Control Orifice with Brass Body.SLDPRT, 50695K61_37 Degree Flared Fitting for Steel Tubing.SLDPRT, 51495K181_Nickel-Plated Brass Push-to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]
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2021-12-28 o-ring re-construction. broke 1/4 tube
    [Rocket.SLDASM, Tube_1-Rocket.SLDASM, Tube_2-Rocket.SLDASM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]
2021-12-29 first iteration burst disk holder
    [AS568-006-O-Ring.SLDPRT, Burst_Assembly.SLDASM, Rocket.SLDASM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]
2021-12-29 integrated fuel bulkhead and pintle core
    [Rocket.SLDASM, Tube_3-Rocket-001.SLDASM, annulus.SLDPRT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]
2021-12-30 cots nozzle and lox tube offset
    [2840K21_316 Stainless-Steel Panel-Mount On Off Valve.SLDPRT, 2840K23_316 Stainless-Steel Panel-Mount On Off Valve.SLDPRT, 4112T53_Compact High-Pressure Brass B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]
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2021-12-31 finalizing pneumatic valve design (last commit of 21!)
    [2333N129_Nickel-Plated Brass Push-to-Connect Fitting.SLDPRT, 51495K179_Nickel-Plated Brass Push-to-Connect Tube Fitting.SLDPRT, 51495K181_Nickel-Plated Brass P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]
2022-01-04 fasteners, clearance holes, pneumatic vent mod
    [92311A345_18-8 Stainless Steel Cup-Point Set Screw.SLDPRT, Engine-Retainer_config.SLDASM, Tube_2-Rocket.SLDASM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]
2022-01-05 vent valve finish, fasteners update, tree cleanup
    [spacer.SLDPRT, vent-valve-piston.SLDPRT]
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2022-01-05 version 1 standalone valve
    [fuel-press-piston.SLDPRT, fuel-press-valve.SLDASM, fuel-press-valve.SLDPRT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]
2022-01-05 adjusting lox pipe for valve space
    [fuel-press-valve.SLDASM, lox-tube-bent.SLDPRT]
2022-01-05 added fuel press valve, position, and clearance
    [Tube_2-Rocket.SLDASM, fuel-press-valve.SLDASM, fuel-press-valve.SLDPRT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]
2022-01-05 added lox fill valve key clearance
2022-01-05 clean unused components from assembly
    [2840K21_316 Stainless-Steel Panel-Mount On Off Valve.SLDPRT, 2840K23_316 Stainless-Steel Panel-Mount On Off Valve.SLDPRT, 4114T43_Brass Panel-Mount On Off Valv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]
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2022-01-06 propagated fasteners features to tubes
    [body_tube.SLDPRT, fiberglass-avionics-tube.SLDPRT, liquid_tube.SLDPRT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]
2022-01-07 drawing updates, made clearance holes whole angles
    [body_tube.SLDPRT, fiberglass-avionics-tube.SLDPRT, liquid_tube.SLDPRT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]
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2022-03-28 created test mold for engine
    [Auto-Main_LOX-Rocket.SLDASM, BOTTOM-cast-with-nozzle_MOLD_chamber-core.SLDPRT, BOTTOM-cast-with-nozzle_MOLD_chamber-core.STL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]
2022-04-02 piston and bulkhead fit adjustment
    [Engine-Retainer_config.SLDASM, spacer.SLDPRT]
2022-05-26 press bulkhead o-rings resizing
    [51495K181_Nickel-Plated Brass Push-to-Connect Tube Fitting.SLDPRT, 5288T266_Oil-Resistant Buna-N Backup Rings.SLDPRT, 7397N12_Universal-Thread Push-to-Connect 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]
2022-05-26 updated pneumatic valve dimensions for new fitting
    [pyro-valve-piston.SLDPRT, spacer.SLDPRT]
2022-05-27 small drawing updates pre pneumatic set screw change
    [body_tube.SLDPRT, fiberglass-avionics-tube.SLDPRT, liquid_tube.SLDPRT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]
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2022-06-26 engine tube resize wip
    [5288T266_Oil-Resistant Buna-N Backup Rings.SLDPRT, body_tube.SLDPRT, fiberglass-avionics-tube.SLDPRT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]
